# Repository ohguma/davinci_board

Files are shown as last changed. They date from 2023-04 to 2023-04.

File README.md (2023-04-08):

# ダ・ヴィンチ32U 拡張基板

## 概要

+ [ストロベリー・リナックス](http://strawberry-linux.com/)の「[ダ・ヴィンチ32U with Arduino Bootloader](http://strawberry-linux.com/catalog/items?code=25005)」の拡張基板。
  + マイコン　ATMEGA32U4。Arduino Leonard 互換。
    + mini-USB な点に注意 
  + アナログ入力12本（A0～A11）が利用可能。電源は5V。
  + 1つのタクトスイッチ（D7） はINPUT_PULLUPで使用する。
  + 複数のI2C端子はTJ3B互換［SCL,5V,SDA,GND］
+ モータードライバ　TB6612FNGを搭載し、モーター2個を制御可能。
  + [TB6612FNG日本語データシート](https://toshiba.semicon-storage.com/info/datasheet_ja_20141001.pdf?did=10661)
  + VM=15V(Max)、1chあたりIout=1.2A(ave)、3.2A(peak)
  + VMはバッテリー電圧
+ 基板サイズ　78 x 93mm、周囲の穴は3.2mm径、5mm間隔
  + [タミヤ ユニバーサルプレート](https://www.tamiya.com/japan/products/70172/index.html)上に取り付け可能。

----
## サンプルスケッチ

+ [sample/](./sample/)  

## マニュアル
+ [Davinci Controller 2022版マニュアル](./documents/Davinci_controller_2022_manual.pdf)
  + バッテリーは6～15Vとすること。マニュアル、基板シルクの16Vは誤り。

## 実装例

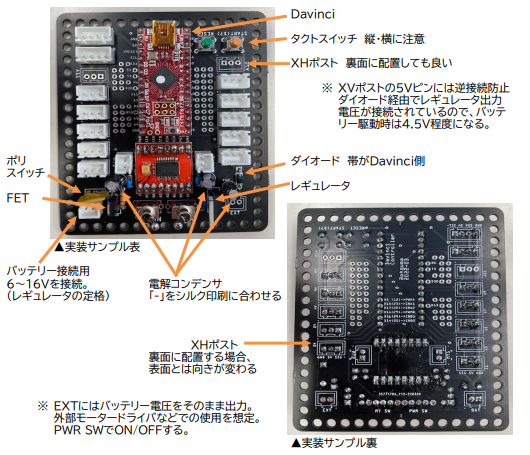
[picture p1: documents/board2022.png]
<br>
▲2022版（バッテリーは6～15Vとすること。上の図は誤り）

----

## パーツリスト

個数は明記なければ1個。☆は取り付け向きに注意。

+ マイコン
  + [ダ・ヴィンチ32U with Arduino Bootloader](http://strawberry-linux.com/catalog/items?code=25005) ☆
+ 入出力関係 ☆
  - タクトスイッチ　1個（D7用） ☆（向きを90度間違えないこと）
  - XH 2ピン用ポスト　任意（バッテリー、モーター2個、バッテリー外部出力(EXT)用） ☆
  - XH 3ピン用ポスト　任意（A0～A11用） ☆
  - XH 4ピン用ポスト　任意（I2C用） ☆
    - XHポストは基板の裏・表どちらに取り付けても良い。
    - 裏面設置時は表の時の逆向きになる。
+ モータードライバ関係
  - [SparkFun Motor Driver - Dual TB6612FNG (1A)](https://www.sparkfun.com/products/14451)☆
    - ピン配置が同じ互換モジュールでもよい。
  - 電解コンデンサ 10V 10uF 2個☆
  - セラミックコンデンサ 35V 0.1uF (104） 2個

+ 電源関連 各1個
  - タクトスイッチ　リセット用　1個☆
  - 基板用トグルスイッチ 2個
    - 下記FETとモーター(TB6612FNG STBY)のON/OFF用
    - モーター用を省略する場合、適宜ジャンパし、TB6612FNG STBYをHIGHにする。
  - PchパワーMOSFET（30V40A MTP4835I3等）☆
  - 抵抗 10KΩ（茶黒橙金）
  - ポリスイッチ　　短絡等の保護用。不要時はジャンパ接続する。

+ 内部5V電源まわり
  - ショットキーダイオード （40V1A 1S4など。レギュレータへの逆接防止用）☆
  - 5Vレギュレータ（5V1A TA4805S等）☆
  - 電解コンデンサ 10V 33uF ☆
  - セラミックコンデンサ 35V 0.1uF (104）

## 購入先
+ [ストロベリー・リナックス](http://strawberry-linux.com/)
  + [ダ・ヴィンチ32U with Arduino Bootloader](http://strawberry-linux.com/catalog/items?code=25005)  
+ [秋月電子](https://akizukidenshi.com/catalog/)
  + 「[ＴＢ６６１２モータドライバ　ブレークアウトボードキット](https://akizukidenshi.com/catalog/g/gK-16947/)」はピン配置が異なるため使用不可。
+ [スイッチ・サイエンス](https://www.switch-science.com//)
  + 「[TB6612FNG搭載 デュアルモータードライバ](https://www.switch-science.com/products/3587)」が「[SparkFun Motor Driver - Dual TB6612FNG (1A)](https://www.sparkfun.com/products/14451)」そのもの。
+ amazonでも見かけるが、値段や送料がべらぼうに高かったり、DRV8833が届いたなどのレビューもあったので要注意。
+ DRV8833のモジュールはTB6612モジュールとピン互換と書かれているものもあるが、DRV8833はモーター1つを2本のPWMで制御する。1本PWMと2本のHIGH/LOWで回転方向を指定する前提の本基板では利用できない。

----
## 回路図

- モータードライバ周りはデータシートの「Typical Application Diagram」に従った。
  - [SparkFun Motor Driver - Dual TB6612FNG (1A)](https://www.sparkfun.com/products/14451)
  - [TB6612FNG Datasheet](https://www.sparkfun.com/datasheets/Robotics/TB6612FNG.pdf)

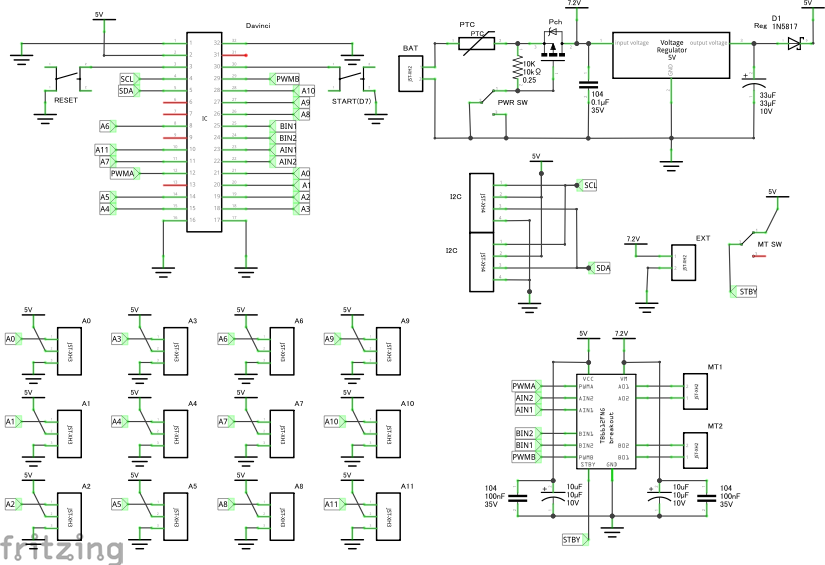
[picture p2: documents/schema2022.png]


| Davinci | TB6612FNG |
| ---- | ---- |
| D15 (23ピン) | AIN1 |
| D17 (22ピン) | AIN2 |
| D5  (12ピン) | PWMA |
| D16 (24ピン) | BIN1 |
| D14 (25ピン) | BIN2 | 
| D11 (29ピン) | PWMB |

| TB6612FNG |　モーター |
| ---- | ---- |
| A01 |　MT1 - |
| A02 |　MT1 + |
| B01 |　MT2 + |
| B02 |　MT2 - |

----
## 基板作成

+ 基板作成は「[JLCPCB](https://jlcpcb.com/)」を利用した。
  + つや消し黒が安い。
  + 2022-03-19発注、2022-09-29到着、運送便はDHLを選択（配達は直接DHLだった）
  + twitter https://twitter.com/JLCPCB_Japan
+ [Fritzingデータ Davinci_controller_2022.fzz](./pcb/Davinci_controller_2022.fzz)
  + [Fritzing](https://fritzing.org/)で設計し、基板作成まで行った。
  + コネクタは表・裏どちらにも実装し易いよう、両面にシルクを入れた。
  + 参考書　 「[Fritzing入門実習テキスト「Fritzing Basics」#マッハ新書 （ダウンロード商品）](https://booth.pm/ja/items/1414214)」
+ [発注時ガーバーファイル order_Davinci_controller_2022.zip](./pcb/order_Davinci_controller_2022.zip)
  + 床センサー基板と一体化したデータで発注してしまったため、追加料金を取られた。
  + 同一パターンの面付けは別料金にならないが、異なるパターンをまとめるとNG

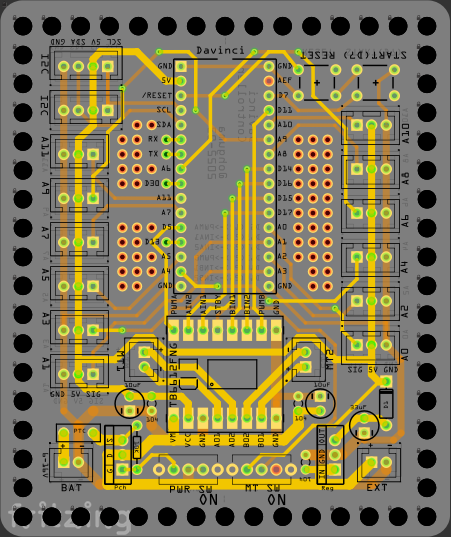
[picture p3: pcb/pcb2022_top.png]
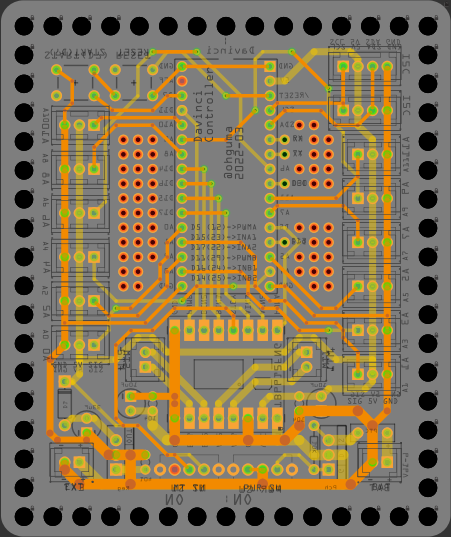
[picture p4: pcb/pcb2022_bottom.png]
 

----

- 2023-04-08 ohguma 誤記など訂正
- 2023-04-05 ohguma 初版

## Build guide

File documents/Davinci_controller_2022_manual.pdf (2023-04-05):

### ■Davinci Controller 2022版

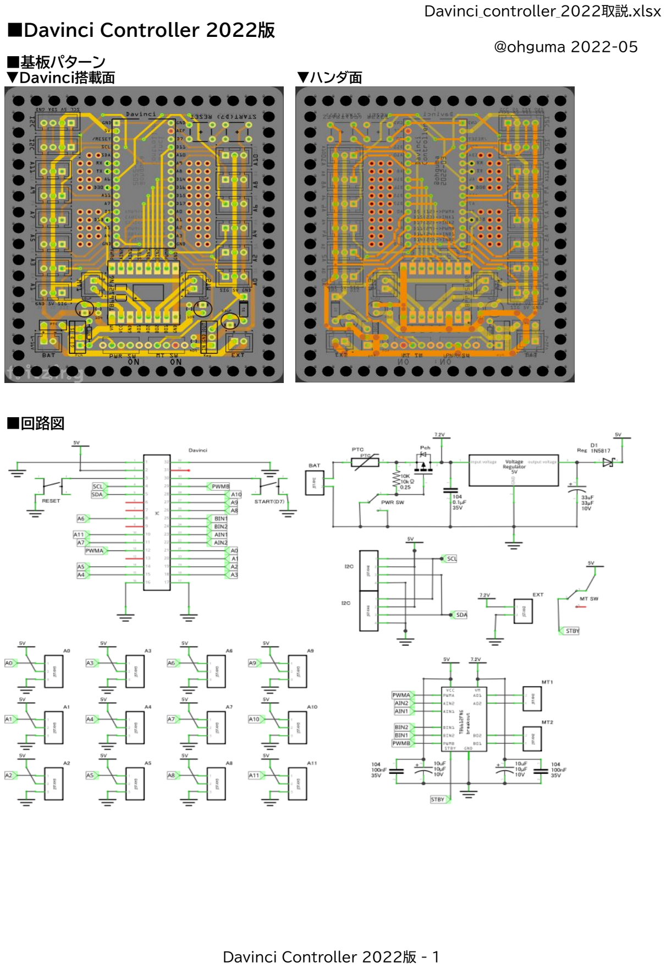
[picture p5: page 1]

Davinci_controller_2022取説.xlsx

@ohguma 2022-05
■基板パターン
▼Davinci搭載面 | ▼ハンダ面

■回路図

Davinci Controller 2022版 - 1

Davinci_controller_2022取説.xlsx ■パーツリスト
種別 | 品名 | 数量
CPU | Davinci 32U with Arduino Bootloader ☆ | 1
モードラ | TB6612FNG モジュール（SparkFun 互換） ☆ | 1
U | 低損失三端子レギュレーター 5V1A （TA4805Sなど） ☆ | 1
Q | PchパワーMOSFET （2SJ681 60V5Aなど） ☆ | 1
D | 整流用ショットキーダイオード （1S3 30V1Aなど） ☆ | 1
F | ポリスイッチ （1.35A (2.7Aで遮断) 耐圧:30V RUEF135など） | 1
C | 電解コンデンサ 10V33μF ☆ | 1
C | 電解コンデンサ 10V10μF ☆ | 2
C | セラミックコンデンサ 35V0.1uF(104) | 3
R | 抵抗 10KΩ | 2
SW | タクトスイッチ　（リセット用、スタート用） | 2
SW | 基板用トグルスイッチ（電源、モータースタンバイ） | 2
CON | B2B-XH-A（2ピン用ポスト　バッテリー、モーターx2、外部用）　※任意 ☆ | 4
CON | B3B-XH-A（3ピン用ポスト　センサー用）　※任意 ☆ | 12
CON | B4B-XH-A（4ピン用ポスト　I2C用）　※任意 ☆ | 2
☆：取付向きに注意すること。極性あり。
Davinci | USBコネクタが基板外側
TB6612FNG モジュール STBYピンがDavinci側
レギュレータ、FET | ラベル面をEXT側に向ける。

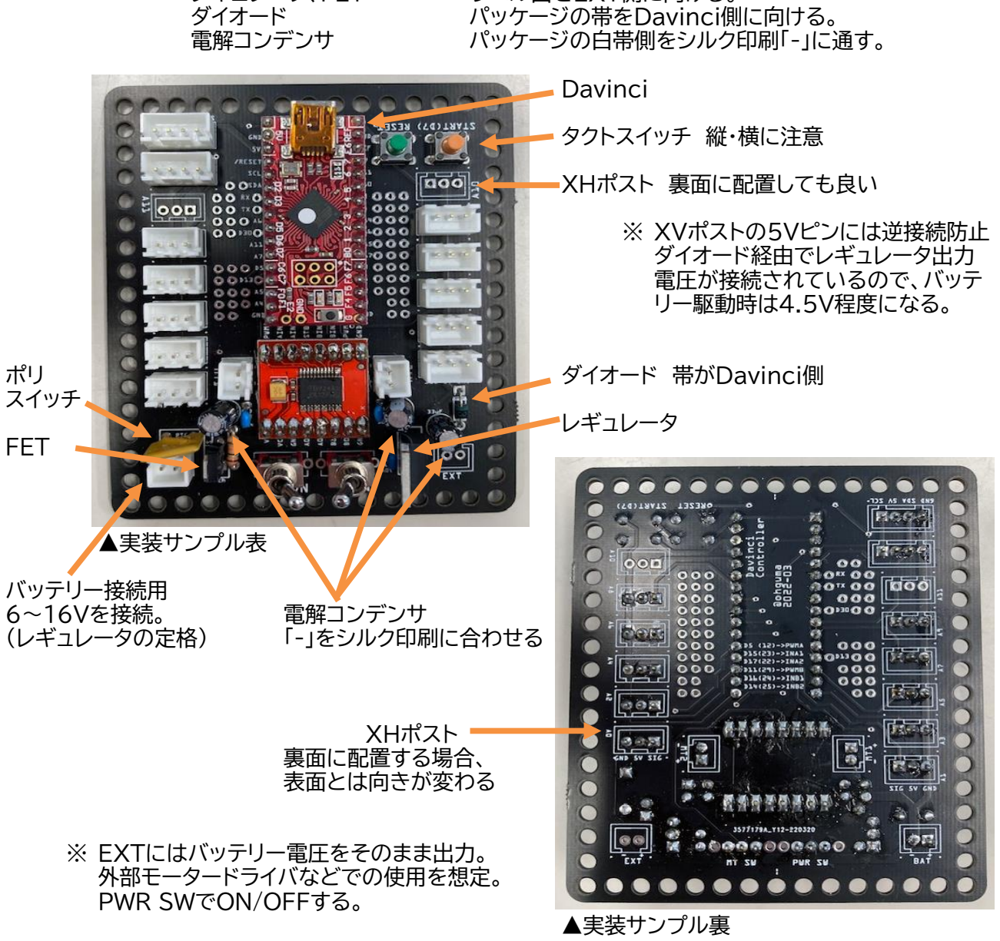
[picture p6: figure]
ダイオード; パッケージの帯をDavinci側に向ける。; 電解コンデンサ; パッケージの白帯側をシルク印刷「-」に通す。; Davinci; タクトスイッチ 縦・横に注意; XHポスト 裏面に配置しても良い; ※ XVポストの5Vピンには逆接続防止 ダイオード経由でレギュレータ出力 電圧が接続されているので、バッテ リー駆動時は4.5V程度になる。; ダイオード 帯がDavinci側; スイッチ; レギュレータ; FET; ▲実装サンプル表; バッテリー接続用; 6～16Vを接続。; （レギュレータの定格）; 「-」をシルク印刷に合わせる; XHポスト 裏面に配置する場合、 表面とは向きが変わる; ※ EXTにはバッテリー電圧をそのまま出力。 外部モータードライバなどでの使用を想定。 PWR SWでON/OFFする。; ▲実装サンプル裏

Davinci Controller 2022版 - 2

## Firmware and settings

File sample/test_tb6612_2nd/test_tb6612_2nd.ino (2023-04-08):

// ダ・ヴィンチ32U 拡張基板
// https://github.com/ohguma/davinci_board
//
// モーターテスト 第２弾 スピード可変
// 2023-04-08 ohguma
//
// ■マイコン情報
// ストロベリーリナックス
// ダ・ヴィンチ32U with Arduino Bootloader
// https://strawberry-linux.com/catalog/items?code=25001
//
// ■ピン設定
// ・スタートスイッチはD7に接続されONでGNDに繋がる。
// ・D7はINPUT_PULLUPモードで使用する。
const int PIN_SW_START = 7;
//
// ・モータードライバ TOSHIBA TB6612FNG
// Davinci             TB6612FNG
// ━━━━━━┓      ┏━━━━━┓
// D15 (23ピン)┠───┨AIN1   A01┠─ MT1 -
// D17 (22ピン)┠───┨AIN2   A02┠─ MT1 +
// D5  (12ピン)┠───┨PWMA      ┃
// D16 (24ピン)┠───┨BIN1   B01┠─ MT2 +
// D14 (25ピン)┠───┨BIN2   B02┠─ MT2 -
// D11 (29ピン)┠───┨PWMB      ┃
//
// IN1  IN2  PWM  動作
// ---- ---- ---- -----------------
// LOW  LOW  HIGH 停止
// HIGH LOW  数値 時計回り
// LOW  HIGH 数値 半時計回り
// HIGH HIGH 任意 ショートブレーキ（モーター端子を短絡した状態）
//   ※数値は0～255で指定する(255指定時が100%)。analogWrite()を使う。
//
// TB6612FNG Hookup Guide
// https://learn.sparkfun.com/tutorials/TB6612fng-hookup-guide/all
//
// MOTOR1
const int PIN_TB6612_AIN1 = 15;
const int PIN_TB6612_AIN2 = 17;
const int PIN_TB6612_PWMA = 5;

void setup() {
  Serial.begin(9600);
  // オンボードLED 出力設定（LED_BUILTINは定義済定数。値は13）
  pinMode(LED_BUILTIN, OUTPUT);
  // スタートスイッチ プルアップ入力設定
  pinMode(PIN_SW_START, INPUT_PULLUP);
  // MOTOR1
  pinMode(PIN_TB6612_AIN1, OUTPUT);
  pinMode(PIN_TB6612_AIN2, OUTPUT);
  pinMode(PIN_TB6612_PWMA, OUTPUT);

  // スタートスイッチが押されるまで、オンボードLEDを点滅する。
  unsigned long tm = 0;
  // スタートスイッチが押されるとINPUT_PULLUPモードの
  // digitalRead()はLOWになり、whileを終了する。
  Serial.println("Wait until the start switch is pressed.");
  while (digitalRead(PIN_SW_START) == HIGH) {
    // tmは500ミリ秒ごとに0,1,2,3,…となる。
    tm = millis() / 500;
    // 500ミリ秒ごとにLEDをON/OFFする。
    if (tm % 2 == 1) {
      // tmを2で割った余りが1の時、LED：ON
      digitalWrite(LED_BUILTIN, HIGH);
      Serial.print("o");
    } else {
      // tmを2で割った余りが0の時、LED：OFF
      digitalWrite(LED_BUILTIN, LOW);
      Serial.print(".");
    }
    //少し待つ。
    delay(100);
  }
  // オンボードLEDが点灯状態のままループしないよう消しておく。
  digitalWrite(LED_BUILTIN, LOW);
  Serial.print("Start loop.");
}

void loop() {
  // 最大スピード設定（％指定）
  int max_speed = 50;
  // スピード設定（％指定）
  int speed = 0;
  // PWM値(0～255)
  int pwm = 0;

  // MOTOR1 前進 加速
  for (speed = 0; speed < max_speed; speed++) {
    digitalWrite(PIN_TB6612_AIN1, HIGH);
    digitalWrite(PIN_TB6612_AIN2, LOW);
    pwm = map(constrain(speed, 0, 100), 0, 100, 0, 255);
    analogWrite(PIN_TB6612_PWMA, pwm);
    Serial.println(speed);
    delay(10);
  }
  // 最大スピード維持
  delay(500);
  // MOTOR1 前進 減速
  for (speed = max_speed - 1; speed >= 0; speed--) {
    // MOTOR1
    digitalWrite(PIN_TB6612_AIN1, HIGH);
    digitalWrite(PIN_TB6612_AIN2, LOW);
    pwm = map(constrain(speed, 0, 100), 0, 100, 0, 255);
    analogWrite(PIN_TB6612_PWMA, pwm);
    Serial.println(speed);
    delay(10);
  }
  // MOTOR1 停止
  digitalWrite(PIN_TB6612_AIN1, LOW);
  digitalWrite(PIN_TB6612_AIN2, LOW);
  digitalWrite(PIN_TB6612_PWMA, HIGH);
  delay(500);
}


//  ■課題
//  (1) シリアルモニタを見ながら、スケッチを実行する。
//  (2) MOTOR1とMOTOR2を同時に同様に動かす。
//

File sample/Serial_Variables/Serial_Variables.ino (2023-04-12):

// シリアル通信・変数のデータ型
// 2023-04-10 ohguma
//
// 本スケッチは変数min_valueで指定した数値から、変数max_valueで指定した
// 数値までを順番に足した合計を5秒ごとに繰り返し表示する。

void setup() {
  Serial.begin(9600);
}

void loop() {
  int min_value = 1;   // 足し始めの数
  int max_value = 10;  // 足し終わりの数
  int sum = 0;         //(足し始めの数)から(足し終わりの数)の和
  for (int i = min_value; i <= max_value; i++) {
    sum += i;  // sum = sum + i;と同じ意味
  }
  Serial.println(sum);  // 合計表示
  delay(5000);  // 5秒停止
}

// ■課題１
// Serial.print()とSerial.println()を使い分けて以下の課題を解くこと。
// それぞれの詳細はArduino リファレンスを参照すること。
//
// (1-1)合計表示を数字だけでなく、数字の前に「Annswer:」の文字列を表示
//      する。
//
// (1-2)for文より上で、(足し初めの数)と(足し終わりの数)を
//        「Sum of 1 to 10」
//      の形式で改行つき表示する。
// 
// (1-3)for文の中で
//        変数iを足す前の変数sum
//        変数i
//        変数iを足した後の変数sum
//      の３項目を順番に「1+2=3」形式で改行付きで表示する。
//
// ■課題２
// (2-1)足し終わりの数を10以外に変更し、結果を確認する。
//      1からnまでを足した合計は次の公式で計算できる。
//        1 + 2 + 3 + … + n = n * (n + 1) / 2
//      
// (2-2)足し終わりの数を1000などに変更した場合でも、(1-3)の途中の計算式
//      が正しく出力されるようにプログラムを修正すること。      
//      Arduino リファレンスのデータ型を参照する。
//      元のプログラムはで「int (整数型)」を使用している。
//
// ■課題３
// (3-1)新しいスケッチを作成し、九九の表を表示する。
//      例「1 2 … 9」
//        「2 4 … 18」
//          ：
//        「9 18 … 81」
// 
// (3-2)九九の結果の1の位の位置を各行で揃えて表示する。
//      例「 1  2 …  9」
//        「 2  4 … 18」
//          ：
//        「 9 18 … 81」
//
// (3-3)九九の表の上・左に見出しをつける。
//      例「  | 1  2 …  9」
//        「--+-- -- … --」
//        「 1| 1  2 …  9」
//        「 2| 2  4 … 18」
//          ：
//        「 9| 9 18 … 81」
// 
// (3-4)九九を１６✕１６まで拡張して表示する。
//      1の位を位置を各行で揃えて表示する。
//      表の上・左に見出しをつける。
// 

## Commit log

2023-04-05 マニュアル追加
2023-04-05 サンプルスケッチ追加
2023-04-06 サンプル更新
2023-04-08 README更新
2023-04-08 サンプル更新。誤記等修正、課題追加。
2023-04-12 サンプル、課題追加
